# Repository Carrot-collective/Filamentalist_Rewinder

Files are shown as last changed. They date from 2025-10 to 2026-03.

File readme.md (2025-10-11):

## Carrot Collective Projects

[ERCF v3](https://github.com/Carrot-collective/ERCF_v3)

[ERCT / CottonTail](https://github.com/Carrot-collective/ERCT)

[Filametrix Toolhead Cutter Buffer](https://github.com/Carrot-collective/Filametrix)

[Blobifier Purge System](https://github.com/Carrot-collective/Blobifier)

[Filamentalist Rewinder Buffer](https://github.com/Carrot-collective/Filamentalist)

### Carrot Collective Affiliates

[Jabberwocky Toolhead](https://github.com/kinematicdigit/Jabberwocky)

[Happy Hare Wiki](https://github.com/moggieuk/Happy-Hare/wiki)

<br />

<p align="center">
<h1 align="center">The "Filamentalist" Passive Filament Driven Rewinder</h1>

[](https://github.com/Enraged-Rabbit-Community/ERCF_v2/tree/master/Recommended_Options/Filamentalist_Rewinder/Filamentalist_Classic_Rewinder)[](https://github.com/Enraged-Rabbit-Community/ERCF_v2/tree/master/Recommended_Options/Filamentalist_Rewinder/Filamentalist_FV3_Rewinder)[](https://github.com/Enraged-Rabbit-Community/ERCF_v2/tree/master/Recommended_Options/Filamentalist_Rewinder/Filamentalist_Enclosure)
</p>
   
## _____ [Filamentalist "Classic"](https://github.com/Enraged-Rabbit-Community/ERCF_v2/tree/master/Recommended_Options/Filamentalist_Rewinder/Filamentalist_Classic_Rewinder) _________ [Filamentalist FV3](https://github.com/Enraged-Rabbit-Community/ERCF_v2/tree/master/Recommended_Options/Filamentalist_Rewinder/Filamentalist_FV3_Rewinder) ___________[Filamentalist Enclosure](https://github.com/Enraged-Rabbit-Community/ERCF_v2/tree/master/Recommended_Options/Filamentalist_Rewinder/Filamentalist_Enclosure) ____
</p>

## Filamentalist Discord group [here:](https://discord.gg/zHGH9sXFVK) ##

##  Description & Theory of operation:

The Filamentalist is a passive (no motors or electronics required) integrated buffering and spool holding multi-material unit (MMU) solution.  It provides space savings and potential filament path reduction that comes with using paths from spool to buffer to MMU.

- The Filamentalist uses the axial force delivered by the MMU gear motor along the filament to load and unload to and from the filament spool.
- An adjustable spring clamp forces the filament against two o-rings that sit on the drive pulley to create a high traction interface for rotating the axle and filament spool.
- A one-way clutch style bearing locks against the drive shaft and rotates the filament spool to take up filament during an unload.
- For loading and print extruding, the clutch disengages allowing for effective free-spooling of the filament spool similar to a roller style spool holder.
- The difference in diameter of the filament driven clutched roller versus the larger rim roller that the filament spool sits on provides the needed gear ratio to produce enough rotations to take up, and unload a nearly empty or full filament roll.
- During unloading/buffering, to account for the varying diameter of a spool from full to empty, filament tension will cause the spring loaded arm to lift a small amount and release traction from the o-rings allowing slip to occur between the filament and the o-ring interface of the rewinder producing a dynamic, continuously modulating variable gear ratio (full spool = max slip, empty spool = no/minimal slip).

<p align="center">

</p>

<p align="center">


</p>

## Filamentalist Version Selection ##

One version is not necessarily better than the other.  The Filamentalist Classic has slightly better Tensioner system geometry making it a bit smoother in the filament grip/slip modulation.  The FV3 is "sexier" and accomodates wider spool widths in less horizontal space which can be useful for fitting in existing enclosures or across the top of a printer.  Below is a selection table to help with your decision.

<p align="center">

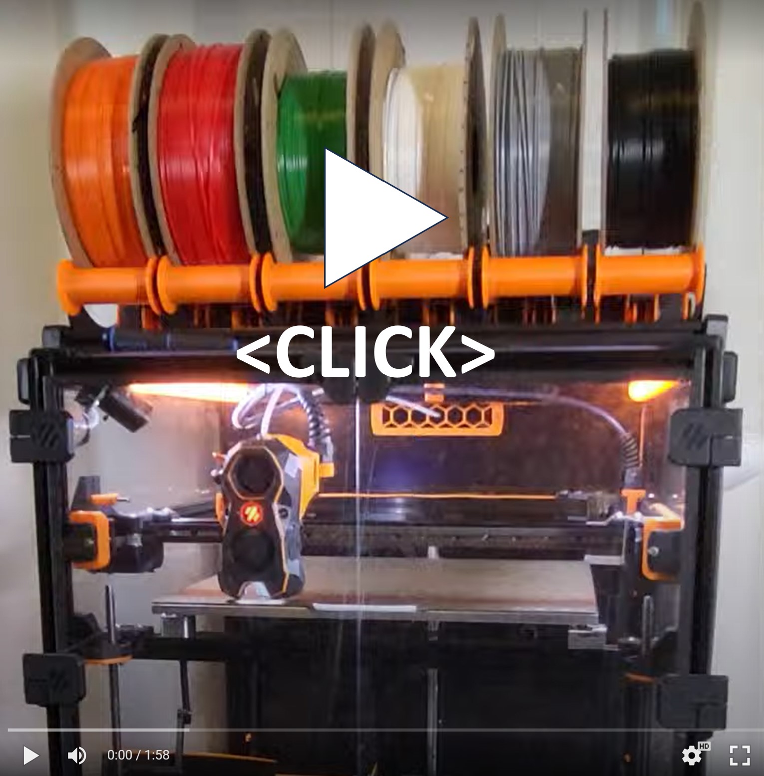
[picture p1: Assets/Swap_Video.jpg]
## Video of 6 rewinders swapping (plus SW Only Blobifier Purging):  [](https://photos.app.goo.gl/hKso7JYPZcdRLKrW8)

## [Video of loading a spool (pre-gate sensors auto-detect filament and pull into ERCF):](https://photos.app.goo.gl/yGS7Rr49dFMvjNLF9)  [](https://photos.app.goo.gl/yGS7Rr49dFMvjNLF9)

##  Credits:
Discord user Thisiscam first made me aware of [Muzi Xiaoyang's video](https://www.bilibili.com/video/BV1ZM41197fX/?spm_id_from=333.337.search-card.all.click) of a filament driven rewinder .  Through a long collaboration with Thisiscam, a great Beta dev/test team, and many design iterations/improvements on the Muzi Xiaoyang design, the Filamentalist was born. Key changes to the Muzi Xiaoyang design include incorporation of a one-way bearing, establishing the correct gear ratio for operation across the range of empty-to-full spools, and the long-life o-ring based filament clamping interface.

A special mention and thanks goes out to Cheesefrog and JCPhlux for their innovation and inputs for design refinement. 

##  **Additional Notes/Considerations** 

Things that you need to know include:
1. Due to continual evolution of the design based on user feedback, the pictures in the readme files and documentation may not always reflect the most current designs.  They will be similar and generally represent the latest parts and assemblies.
2. There are multiple options for the Filamentalist.  Determine which versions/options you want and select the stl's to print accordingly.  If you use Autodesk Fusion 360 there is parametric models available for both the Classic and FV3 rewinders that will allow customization for unique widths and axle lengths. Please see the Selection Aid table above to help choose.
3. If you're using, or upgrading from a ERCFv1 or v2 version you may want/need a higher torque gear motor.  Many in the Beta team ran NEMA 17's spec'd at 55 N-cm max torque and config'd them for 1-1.5A (probably overkill...).  If running the ERCF V1 or V2 with the 80 tooth gear Grafton's [40 Tooth NEMA 17 Mod](https://www.printables.com/model/692720-ercf-40-tooth-gear-modifiction) is a good modification for gaining more speed from a motor with 40N-cm torque or greater.  This may not be required so if you already have built your ERCF, try the Filamentalist with the motor/gearing you have and decide if you think you need more torque/speed.
4. Because the standard tuning of this design relies on some filament slip at the o-rings, the o-rings may ultimately wear-out.  Testing and extrapolation estimates that the wear-out point is  greater than 5K cycles. See the O-Ring Replacement section in the assembly manuals for o-ring swap/replacement instructions. 
5. Due to pressfits for the axle bearings and ECAS fitting, printer calibration is important.  Calibration "Test Block" stl's are included in the projects/CAD.  It is recommended you print the calibration tool first and test the press fits, M3 thread cutting, M3 slip fit, filament path holes to determine if you need to apply any scaling or changes to your extrusion factors in your slicer before printing.  Due to varying ECAS supplier tolerances and varying printer tolerances some experienced cracking at the ECAS hole when pressing in the ECAS.  If all other press fits work well on the calibration tool but you experience cracking at the ECAS hole when pressing in an ECAS fitting, you can use an Xacto knife to lightly remove some plastic from the ECAS hole.  If the ECAS is too loose you can use superglue to glue the ECAS into the Tensioner Mount (not the Test Block 😉 ).
6. Questions or input?
   - Refer to the [FAQ](https://github.com/Enraged-Rabbit-Community/ERCF_v2/blob/master/Recommended_Options/Filamentalist_Rewinder/Filamentalist_FAQ.md)
   - [Troubleshooting Guide](https://github.com/Enraged-Rabbit-Community/ERCF_v2/blob/master/Recommended_Options/Filamentalist_Rewinder/troubleshoot.md)
   - Filamentalist Discord group [here:](https://discord.gg/zHGH9sXFVK)

##  Tuning

Tune by setting the Tensioner Arm clamping force.  The arm does not need an extreme amount of tension.  To tune the spring force, lift the tensioner and insert a section of filament through the o-ring bearing interface and into the bowden tube.  Hold a Rim Roller to keep it from rotating and try to pull the filament out (in unload direction).  You want the slip force to be slightly more than what the overall system drag is, so you have to imagine the range of gear motor pull force vs rewinder drag and set a slip range in-between the two "imaginary" lines.  As a starting point adjust the spring tensioner screw accordingly and err on the light side.  Run the rewinder (see test code below). If loose filament is forming around the filament spool during unload, tighten the spring tensioning screw.  If no loose filament is forming around the filament roll, gradually reduce the spring tension until loose filament starts to accumulate and then increase tension in ~1/2 screw turn increments until you feel you have the lightest tension that results in a tightly packed unload. 

##  Testing

Below are macros you can cut and paste into the bottom of your mmu_software.cfg or printer.cfg to test and tune your rewinders.

Happy multi-material printing and rewindering!

```
[gcode_macro rewinder_test]
gcode:
    {% set tool = params.TOOL | default(0) | int %}   ; This target can be set with the drop-down in Mainsail
    {% set cycles = params.CYCLES | default(5) | int %}   ; This target can be set with the drop-down in Mainsail
    {% set speed = params.SPEED | default(300) | float %}   ; This target can be set with the drop-down in Mainsail
    {% set accel = params.ACCEL | default(300) | float %}   ; This target can be set with the drop-down in Mainsail
    {% set length = params.LENGTH | default(800) | float %}   ; This target can be set with the drop-down in Mainsail

    MMU_SELECT TOOL={tool}
    MMU_PRELOAD
    MMU_TEST_LOAD LENGTH=50
    {% for n in range(cycles) %}

        MMU_SERVO POS=DOWN
        MMU_TEST_MOVE SPEED={speed} ACCEL={accel} MOVE={length}
        MMU_SERVO POS=UP
# to stop a macro mid-cycle you must use the e-stop.  This dwell allows you to hit the e-stop while the servo is up so that you can pull the filament out of the ERCF while the printer/macro is stopped
        MMU_SERVO POS=DOWN
        MMU_TEST_MOVE SPEED={speed} ACCEL={accel} MOVE=-{length}
        MMU_SERVO POS=UP

    {% endfor %}

    MMU_UNLOAD

```

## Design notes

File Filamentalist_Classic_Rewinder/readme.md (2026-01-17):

<p align="center">
<h1 align="center">The Filamentalist "Classic" Passive Filament Driven Rewinder</h1>

<p align="center">]
</p>
   
## [Filamentalist Classic Assembly Guide Document](https://github.com/Enraged-Rabbit-Community/ERCF_v2/blob/a68bc6678bab41d7bded5e42a17276a9430a0f45/Recommended_Options/Filamentalist_Rewinder/Filamentalist_Classic/Do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)  [](https://github.com/Enraged-Rabbit-Community/ERCF_v2/blob/a68bc6678bab41d7bded5e42a17276a9430a0f45/Recommended_Options/Filamentalist_Rewinder/Filamentalist_Classic/Do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)

## [Filamentalist Classic Assembly Guide Video](https://youtu.be/-1cHOcnosxE?si=RZV318OI9f3f_CkE)  [](https://youtu.be/-1cHOcnosxE?si=RZV318OI9f3f_CkE)

##  **BOM:**

**ATTENTION!! PLEASE READ COMMENTS IN FAR RIGHT COLUMN** (you may need to scroll over in your view)

| Qty per Site | Part | Example Source Reference | Comments |
|---|---|---|---|
| 1 | 8mm dia. x 80mm Stainless Steel Dowell Pin | https://www.amazon.com/uxcell-Stainless-Chamfered-Support-Elements/dp/B0BC8VFSWD, Amazon Alternate https://www.amazon.com/Unifizz-Stainless-Steel-Round-Silver/dp/B09P9MC953?th=1 (sheared ends may need to be cleaned up), Aliexpress https://www.aliexpress.us/item/3256801518620991.html | Undersized shaft (7.93-7.97mm or 5/16" dia) works the best.  100mm length is more available and can extend out of rewinder, you can cut polished 8mm or 5/16" diameter stainless rod to length, or there are stls to make a wider rewinder based on a 100mm axle.  Custom rewinder widths are also possible using the Fusion 360 parametric model and you can cut shaft to whatever length is desired. 8mm (or 5/16") diameter straight stainless tube is also an excellent alternative to solid rods as the are much easier to cut to length. |
| 5 | MR608 bearings | Can be obtained anywhere (Home Depot, Amazon, Aliexpress, etc.)  | Inexpensive MR608-2RS rubber dust seal style is recommended as they are slightly higher resistance than the open, ZZ metal seal style, or plastic bearings. You actually want a little of resistance in the axle bearings to help the 1-way bearing unlock. |
| 1 | HF081412 One-Way Bearing | https://www.amazon.com/dp/B0C7TRFJBS, Aliexpress | 8mm Bore, 12mm length, 14.2mm Diameter. Get the "octogonal" style. |
| 1 | ECAS press-in pneumatic fittings for the bowden tubes (like used in ERCF)  |  | A locking clip is required and can be bought or printed (stl included).  The rubber seal is not needed and should not be installed upon assembly. |
| 2 | O-rings | Metric 3.5x20 (ID) or AS568 Standard size 211, Home Depot #110, Amazon example: https://www.amazon.com/211-Buna-N-Ring-Durometer-Black/dp/B000FN0W7I/, Aliexpress example: https://www.aliexpress.us/item/2255799953260685.html (select correct size) | In the range of 13/16" ID, 1-1/16" OD or ~20mm ID, ~27mm OD, ~3.5mm cross section/cs, Nitrile Butadiene Rubber (NBR or Buna-N)|
| 1 | Spring  | https://www.amazon.com/dp/B076LNJF5Q, Aliexpress | Like in extruders - 304 Stainless Steel,6mm OD,0.6mm Wire Size,7.5mm Compressed Length,15mm Free Length (the stiffer 1mm wire size extruder spring used on CW2 and G2E will also work if you have those on-hand) | |
| 1 | 3mm Heatset Insert | M3x4x5 like these:  https://www.amazon.com/gp/product/B09MCW7ZN5 | Voron standard size | set into the Tensioner Mnt |
| 1 | 3x35mm SHCS | SS Socket Head Cap Screw | Spring Tensioner Screw anything in the range of 35mm +/- 10mm should work.  If building the alernate reverse access version then a 30mm length is recommended. |
|  2-6  | M3x8 SHCS  |  Stainless Steel Socket Head Screw | for locking rim rollers to 8mm steel axle shaft.  1 to 3 screws per roller Depending on tightness/looseness of Rim Roller center bore |
| 6 | 3x12 FHCS  |  Stainless Steel Flat Head Screw | for Tensioner Mnt and Rear Axle installation 8/10/12mm lengths will work|
| 3 | 3x18 FHCS  |  Stainless Steel Flat Head Screw | for Tensioner Arm clamp bearings and Tensioner Mnt pivot installation 16mm length will work |
| 1 | M3 Washer  |  Stainless Steel | between Spring Tensioner screw head and spring |
| 4 | Rubber Band | See [FAQ](https://github.com/Enraged-Rabbit-Community/ERCF_v2/blob/master/Recommended_Options/Filamentalist_Rewinder/Filamentalist_FAQ.md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)) | bike tire inner tube or rubber bands |

**Optional Parts**
| Qty per Site | Part | Example Source Reference | Comments |
|---|---|---|---|
| 1 | D2F-L3 Microswitch  | Omron brand - Mouser, Digikey, etc., Aliexpress example: https://www.aliexpress.us/item/3256805036222979.html  | for pre-gate sensor option versions |
| 2 | M2x10 Self Tapping Screw | Philips or socket head.  Amazon example: https://www.amazon.com/DTGN-M2x10mm-Phillips-Self-tapping-Screw/dp/B0CSRTYBLR, Aliexpress example: https://www.aliexpress.us/item/3256802486141312.html (select size) | for pre-gate sensor option versions |
| 1 | JST-XH 2-pin Socket/Plug | Amazon example:  https://www.amazon.com/CQRobot-Connector-Terminals-Housing-Adapter/dp/B0B2R966ZY, Aliexpress Example: https://www.aliexpress.us/item/3256804799083128.html (need housing, plug, and terminal) | for pre-gate sensor option versions |
| var. | 24 awg wire  | | for pre-gate sensor option versions |
| var.  | 2.5mm ID PTFE tubing | Amazon, Aliexpress, 3D printing vendors | 2.5mm ID recommended but you can try whatever you have.  Length depends on the distance from your rewinder location to your ERCF inputs |

##  Printing Guidelines:

## **General:**
- Material: ABS or ASA (~170 gm per site)
- Print Time: ~8hr 17min (based on the Ellis PIF profile speeds, accelerations, and volumes)
- 0.2mm layer height
- 40% infill recommended.  Linear style infills are fastest (rectilinear, monotonic, grid, triangles, stars, etc.)
- Wall Count: 4
- Solid Top/Bottom Layers: 5

## **Part Specific:**
- Orientation suggestions are relative to the installed assembly orientation and are shown in the slicer images below.
- There are stls for both 80mm and 100mm wide version and a Fusion 360 parametric CAD model for additional custom widths.  See "Additional Notes/Considerations" point 3 above for more details.
- If rotating the Filamentalist is not feasible for your required filament loading direction or you need a bottom feed capability (for example enclosure limitations or feeding through the bottom of a shelf) there is an option for a rear loading version which only requires printing the Tensioner_Mount_Rear_Load_80mm/100mm_[option] in the place of Tensioner_Mount_80mm/100mm part.
  
  

- Stl's are provided for optional clip-in style supports where no Base_Plate is needed and the rewinders are easily clipped in and out of (2) 2020 extrusions mounted 170mm center-to-center apart.  This option is highly recommeded if your setup can accomodate this style type of mount.
  
  
- **!! IMPORTANT !!  This design relies on multiple press-fits for bearings and ECAS fittings.  As a result, printer calibration is important.  A Test_Block stl is included.  It is highly recommended that you print this block first, check fits, and make adjustments to extrusion multipliers and/or slicer scaling if needed before printing the Filamentalist parts.**
  
    

| **Qty per Site** | **Part**  | **Pic** |  **Orientation** | **Printed Supports Needed** | **Comments** |
|---|---|---|---|-----|---|
| 1 | Right_Support |  |  Horizontal | N | |
| 1 | Left_Support |  | Horizontal | N | |
| 1 | Option: Right_Support_[2020_Clip-In_option] |  |  Horizontal | N | |
| 1 | Option: Left_Support_[2020_Clip-In_option] |  | Horizontal | N | |
| 1 | Base_Plate_80mm/100mm_[option] |  | Horizontal | N | Optional part for a standalone unit not mounted to another surface  |
| 1 | Idler_Roller_Axle_80mm/100mm  |  | Horizontal | N | align flat of "D" to build plate |
| 2 | [a]_Rim_Roller_80mm/100mm |  | Horizontal | N | Dished side up. |
| 1 | [a]_Center_Drive_Roller  |  | Horizontal | N | Recommend scattered seams for press fit-bore concentricity |
| 2 | CDR_Spacer_80mm/100mm |   | Horizontal | N | |
| 1 | Tensioner_Arm_Left |   | Horizontal |  N |  |
| 1 | Tensioner_Arm_Right |   | Horizontal |  Built-in | Remove built-in support from the locking tab |
| 1 | [a]_Tensioner_Mount_80mm/100mm |  | Vertical (as installed) | N  | There is a pre-gate sensor option version available as well (split to parts in slicer for print-in-place breakaway connector retaining key).  |
| 1 | [a]_Tensioner_Mount_Rear_Load_80mm/100mm _[option] |  | Vertical (as installed).  Optional for rear loading if needed. | N  | There is a pre-gate sensor option version available as well.  |
| 1 | [a]_Idler_Roller _(male) _80mm/100mm |   | Vertical  | N  |  Scattered seams |
| 1 | [a]_Idler_Roller _(female)_80mm/100mm |   | Vertical  | N  |  Scattered seams |
| 1 | Axle_Depth_Tool_80mm/100mm |  | Vertical | N | Pocket opening up.  Print with 100% infill for reuse strength and durability when building multiple rewinders. |
| 2 | [a]_ECAS_Clip |  |  Horizontal | N | Tab up |
| 1 | Test_Block |  |  608 Pocket facing up | N | printer calibration tool |

##  Tuning

Tune by setting the Tensioner Arm clamping force.  The arm does not need an extreme amount of tension.  To tune the spring force, lift the tensioner and insert a section of filament through the o-ring bearing interface and into the bowden tube.  Hold the center roller by placing your thumb against the o-rings and try to pull the filament out.  You want the slip force to be slightly more than what the overall system drag is, so you have to imagine the range of gear motor pull force vs rewinder drag and set a slip range in-between the two "imaginary" lines.  Adjust the spring tensioner screw accordingly and err on the light side.  Run the rewinder (see test code below). If loose filament is forming around the filament spool during unload, tighten the spring tensioning screw.  If no loose filament is forming around the filament roll, gradually reduce the spring tension until loose filament starts to accumulate and then increase tension in ~1/2 screw turn increments until you feel you have the lightest tension that results in a tightly packed unload. 

##  O-Ring Replacement

You may never need to replace o-rings.  Testing and extrapolation estimates that the wear-out point is ~5K cycles.  The impact of o-ring wear-out can be reduced by periodically swapping highly used rewinders with low use rewinders in your line-up.  Also, o-rings with grooves worn in them can be swapped with their opposing partners to present the unworn side/face to the filament to extend the life of a set.  For o-ring replacement, remove the Drive Roller Assembly from the rewinder (unscrew the (6) screws of the Right and Left Supports).  Then unscrew the set screw on one Rim Roller.  You can now slide the CDR Spacer and Center Drive Roller from the axle, remove the old o-rings (a dental pic works great), and install a pair of new ones.  Reinstall the Center Drive Roller and CDR Spacer back on the axle and install the Rim Roller back onto the axle per 3.3 above, and re-install the supports.  

##  Troubleshooting

Please see [troubleshooting guide](troubleshoot.md), reference the [FAQ](Filamentalist_FAQ.md), or join our discord server (https://discord.gg/uDcGxukRKd) for more help.

#  Version History

Versioning convention.  V"X"."Y"."Z"
- "X" represents a major change in form, fit, or function.  An increment in "X" may not require that existing built units undergo rework but the new parts will generally not be compatible with past version rewinders.
- "Y" represents a "step rev" or minor revision.  These are generally small "tweaks" for improved functionality, useability, and/or assembly and typically would not require reprint/rework for existing rewinders.  
- "Z" represents a backwards compatible "bug fix".  This will generally be addressing nuisance CAD or printability issues.

V1 - 5/17/24 - Public release into ERCF V2 RC2 repository

V1.1 - 5/19/24 - Update to CAD and stls for Tensioner Arms to remove potential filament catching point during endless spool ejection

V1.2 - 5/20/24 - Reverted Center_Drive_Roller to cylindrical press fit hole (vs hex of V1 and V1.1).  Revised 608 press fit pockets of Idler_Roller_(male&female) parts for both 80mm and 100mm width versions for improved press fit.

V1.3 - 5/20/24 - Added bevel to internal step on  Idler_Roller_(male) part for 80mm and 100mm versions to improve printability.  Updated the .f3dparametric file, step files, and stls for 80mm and 100mm versions.

V1.4 - 5/21/24 - Shortened threads on Idler_Roller_male parts by 1.5mm to remove slight interference.  Updated CAD, 80mm, and 100mm stls.

V1.5 - 6/4/24 - Slightly deepened 608 bearing pockets in Idler Roller parts to prevent potential side loading binding due to print/assembly tolerances.  Reprint not required for existing functioning units.

V1.6 - 6/12/24 - No mandatory reprints/rebuilds required:  Updated CAD parametric model and 80/100mm step files because two  Tensioner Mount-to-Support holes were getting "buried" in the 100mm version.  Updated the Tensioner_Mount_100mm stl file as well.

V1.7 - 6/13/24 - Opened up c-sunk hole on Tensioner_Arm_Left part pivot screw hole to allow for full seating of a FHCS head and use of a 16mm long screw.  A new stl for Tensioner_Arm_Left ans new f3d and step files are included.

V1.8 - 7/2/24 - Removed notch/gap in axle pressing tool that shouldn't have been there.  80/100mm stl's updated as well as f3d and stp CAD files.

V2 - 7/22/24
  1. Added Rear Load option Tensioner_Mount (works as bottom load too)
  2. Removed threaded Rim Roller option and converted Rim Rollers from press-fit to set screw style.
  3. Add 608 bearing inner race clearance back into Supports.
  4. Added ~2mm of additional bowden capture in Tensioner_Mounts

V3 - 8/5/24
  1.  Add options for Tensioner Mounts with pre-Gate sensors
  2.  Included option for the Filamentalist Enclosure style Base Supports
  3.  Updated all supports to include a spool guide rail to help keep spools from wandering off of the rollers.

V3.0.1 - 8/8/24 - No reprint/rebuild required:
1. Improved clearances for indexing tab feature in Tensioner Arm parts
2. Improved breakaway feature for small print-in support in Tensioner_Arm_Right part 
3. Provided additional edge chamfering to Idler Roller Axles
4. Reinstated design history in Filamentalist_(parametric)_V3.f3d CAD model so that the parametric functionality would work correctly.
5. Added accent color to file naming convention in stl file names.
6. Updated pdf manual to reflect/describe accent color for file naming convention in stl file names.

V3.0.2 - 8/15/24 - No reprint/rebuild required:
1. Added more reference dimensions to the User Parameters section for the Filamentalist_(parametric).f3d parametric CAD model.

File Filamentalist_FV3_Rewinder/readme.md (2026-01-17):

<p align="center">
<h1 align="center">The Filamentalist V3 ("FV3") Passive Filament Driven Rewinder</h1>
<p align="center">

</p>

## [FV3 Assembly Guide Document](https://github.com/Enraged-Rabbit-Community/ERCF_v2/blob/master/Recommended_Options/Filamentalist_Rewinder/Filamentalist_FV3_Rewinder/Documentation/Filamentalist_V3_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)  [](https://github.com/Enraged-Rabbit-Community/ERCF_v2/blob/master/Recommended_Options/Filamentalist_Rewinder/Filamentalist_FV3_Rewinder/Documentation/Filamentalist_V3_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)
##  **BOM:**

**ATTENTION!! PLEASE READ COMMENTS IN FAR RIGHT COLUMN** (you may need to scroll over in your view)

| Qty per Site | Part | Example Source Reference | Comments |
|---|---|---|---|
| 1 | 8mm dia. x ##mm Stainless Steel Rod, Tube, or Dowell Pin | https://www.amazon.com/uxcell-Stainless-Chamfered-Support-Elements/dp/B0BC8T7ZQB?th=1, Aliexpress https://www.aliexpress.us/item/2255800287548941.html (select M8x70mm) | Undersized shaft (7.93-7.97mm or 5/16" dia) works the best.  50mm axles will work in the standard width design but longer axles cut to length (up to ~75mm) will provide greater stability for the Rim Rollers.  The Classic Filamentalist 80mm axles will work but hang over ~1mm per side.  Custom rewinder widths are possible using the Fusion 360 parametric model and you can cut shaft to whatever length is desired.  8mm (or 5/16") diameter straight stainless tube is also an excellent alternative to solid rods as they are much easier to cut to length like https://www.amazon.com/uxcell-Stainless-Thickness-Seamless-Straight/dp/B081GBTQGC or https://www.aliexpress.us/item/3256805495613016.html. |
| 1 | 688 bearing | For Tensioner Arm|
| 4 | 608 bearings | For Drive and Idler axles.  Can be obtained anywhere (Home Depot, Amazon, Aliexpress, etc.)  | Inexpensive MR608-2RS rubber dust seal style is recommended as they are slightly higher resistance than the open, ZZ metal seal style, or plastic bearings. You actually want a little of resistance in the axle bearings to help the 1-way bearing unlock. |
   OR:
|   4   | 688 bearings | As an alternative to the 608 bearings for Drive and Idler axles, so would be a total of 5 688 bearings including the Tensioner Arm bearing.  This allows for only needing to buy one bearing size but the 688's might be a tighter fit on the axle shafts.  Inexpensive MR688-2RS rubber dust seal style is recommended as they are slightly higher resistance than the open, ZZ metal seal style, or plastic bearings. You actually want a little of resistance in the axle bearings to help the 1-way bearing unlock. |
|   1   | HF081412 One-Way Bearing | https://www.amazon.com/dp/B0C7TRFJBS, Aliexpress | 8mm Bore, 12mm length, 14.2mm Diameter. Get the "octogonal" style. |
|   1   | ECAS04   |  | Press-in pneumatic fitting for the bowden tubes (like used in ERCF).  A locking clip is required and can be bought or printed (stl included).  The rubber seal is not needed and should not be installed upon assembly. |
|   2   | O-ring | Metric 3.5x20 (ID) or AS568 Standard size 211, Home Depot #110, Amazon example: https://www.amazon.com/211-Buna-N-Ring-Durometer-Black/dp/B000FN0W7I/, Aliexpress example: https://www.aliexpress.us/item/2255799953260685.html (select correct size) | In the range of 13/16" ID, 1-1/16" OD or ~20mm ID, ~27mm OD, ~3.5mm cross section/cs, Nitrile Butadiene Rubber (NBR or Buna-N)|
|   1   | Spring  |  https:https://www.amazon.com/dp/B076LNJF5Q, Aliexpress https://www.aliexpress.us/item/3256805126192641.html (select size per comments) | 304 Stainless Steel,6mm OD,0.6mm Wire Size,7.5mm Compressed Length,15mm Free Length |                                 |
|   1 | 3mm Heatset Insert | M3x4x5 like these:  https://www.amazon.com/gp/product/B09MCW7ZN5 | Voron standard size | set into the Tensioner Mnt |
|   1   | M3x30mm SHCS | SS Socket Head Cap Screw | Spring Tensioner Screw |
|  6-10  | M3x12-16mm SHCS  |  12-16mm length will work | for locking rim rollers to 8mm steel axle shaft.  1 to 3 screws per roller Depending on tightness/looseness of Rim Roller center bore.  4 additional screws if using the Filamentalist Enclosure Mounts |
|  4  | M3x12 FHCS  |  Flat Head Cap Screw | for Idler Roller wheels, Tensioner Bearing axle, and Tensioner Pivot |
|   12-14   | M3x8mm FHCS  |  Stainless Steel Flat Head Cap Screw | Qty 12 for 2020 center mount, 14 for Enclosure mount |
|   1   | M3 Washer  |  Stainless Steel | for Spring Tensioner screw |
|   4   | #84 Rubber Band | See [FAQ](https://github.com/Enraged-Rabbit-Community/ERCF_v2/blob/master/Recommended_Options/Filamentalist_Rewinder/Filamentalist_FAQ.md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) | 2" bike tire inner tube cut to width or rubber bands |

**Parts for Microswitch Option**
| Qty per Site | Part | Example Source Reference | Comments |
|---|---|---|---|
| 1 | Omron D2F-01FL-D3 Lever Microswitch | https://www.mouser.com/ProductDetail/Omron-Electronics/D2F-01FL-D3?qs=i1w9Bv2NFd2YXdp4zNwbgA%3D%3D  | For pre-gate sensor levered switch option. |
   OR:
|   1   | Omron D2F-01F-D3 Button Microswitch | https://www.mouser.com/ProductDetail/Omron-Electronics/D2F-01F-D3?qs=i1w9Bv2NFd2sPdBLm34BPQ%3D%3D  | For pre-gate sensor printed lever switch option. |
|   1   | MR85 Bearing | Amazon: https://www.amazon.com/dp/B07CKL54RS, Aliexpress: https://www.aliexpress.us/item/3256807026256776.html   | ZZ, RS, or open style will work.  For pre-gate sensor switch option. |
   OR:
|   1   | 8x3 Disc Magnet | Amazon: https://www.amazon.com/FINDMAG-Magnetic-Whiteboard-Refrigerator-Magnets-8x3mm/dp/B0863BGG6H, Aliexpress: https://www.aliexpress.us/item/3256806495856656.html   | For pre-gate sensor switch option. |
   OR:
|   1   | 6x3 Disc Magnet | Amazon: https://www.amazon.com/TRYMAG-Magnets-Refrigerator-Whiteboard-Neodymium/dp/B09QHSB2XM, Aliexpress: https://www.aliexpress.us/item/3256807048616464.html   | For pre-gate sensor switch option. |  
|   var.   | 24 awg wire  |   | for pre-gate sensor option versions |
|   2   | M2x8mm SHCS |  Amazon:  https://www.amazon.com/Alloy-Steel-Socket-Screws-Black/dp/B015A37DVU, Aliexpress:  https://www.aliexpress.us/item/3256806889548681.html | Self tapping screws can be used as an alternative |
| 2  | Male/Female connectors |  | Connectors of your choice, JST-XH 2-pin works well |

##  Printing Guidelines:

## **General:**
- Material: ABS or ASA (2020 Center Mount version: ~154gm per unit, Filamentalist Enclsoure Mount Version: ~175gm per unit)
- Print Time: 2020 Center Mount version: ~7hr 34min, Filamentalist Enclsoure Mount Version: ~9hr 10min (based on the Ellis PIF profile speeds, accelerations, and volumes)
- 0.2mm layer height
- 40% infill recommended.  Linear style infills are fastest (rectilinear, monotonic, grid, triangles, stars, etc.)
- Wall Count: 4
- Solid Top/Bottom Layers: 5

- Recommended orientation is set in the stl files and should load correctly into slicer programs.  Print orientation is shown below in the slicer plate pictures for base and accent color parts.
- Where applicable, stl's are provided for two different axle bearing types, 688 (16mm OD) and 608 (22mm OD) bearings.  Bearing size is denoted in the file naming.
- **!! IMPORTANT !!  This design relies on multiple press-fits for bearings and ECAS fittings.  As a result, printer calibration is important.  The Print_Calibration_Tool_###_Bearing.stl file is included.  It is highly recommended that you print this part first, check fits, and make adjustments to extrusion multipliers and/or slicer scaling if needed before printing the Filamentalist parts.**
   - Other materials such as PETG or PLA may work fine but parts were not designed or validated for these materials.  If you want to use a different material start with the Print Calibration Tool and adjust extrusion rates and slicer scaling to achieve the correct dimensions for the press fit parts.



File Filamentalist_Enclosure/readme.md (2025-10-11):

# The "Filamentalist" Enclosure # 

The Filamentalist Enclosure is a passive dry box designed to house the Filamentalist passive rewinder.  It  consists of (4) printed endcaps, (6) pieces of 2020 extrusion cut/ordered to the desired length, and 0.060" (1/16') polycarbonate sheet(s) cut to size. Enclosure specific Filamentalist supports are required (these are included in the Filamentalist optional stl's as well as under the Enclosure stl directory).


</p>


</p>


</p>


</p>


</p>


</p>

BOM:

- 2020 Extrusion - Qty 6 - Select/cut length to be greater than or equal to [Rewinder Qty] X [Rewinder Width] + 10mm
    - for example: 6 X 81.5 (std. Filamentalist Width) + 10 = 499mm.  Round up to a standard 500mm long 2020 extrusion
    - get extrusions with holes that can be tapped to a 5mm thread (like the Misumi with a 4.2mm D hole)
    - examples: https://www.amazon.com/dp/B09DYMCBYF, https://www.aliexpress.us/item/3256801651139612.html

- Polycarbonate Sheet (Lexan) - 1/16" (also 0.060" or 1.5mm) thick.  Width of pieces = Extrusion Length -2mm (i.e. cut sheet to 498mm wide if using 500mm extrusions)
    - Lid Length = 451.5mm
    - Base Rear Panel Height = 120mm
    - Base Front Panel Height = 45mm
    - Bottom Panel Length (if used) = 230mm
    - For enclosures up to 607.6mm wide a single 24" x 36" sheet is enough material.
      - (2) 24" x 24" or (1) 24" x 24" + (2) 12" x 24" sheets will work as well if it is easier for you to source smaller sheets.
    - Sourcing Alternatives:
      - If there are difficulties sourcing the recommended Polycarbonate (Lexan) sheet material, PET and PET-G sheet has been used successfully although it wil be less scratch resistant
      - 2mm sheet can also be substituted but it will be more difficult when bending the lid panel into the lid frame and end caps

- Seal Material - ~10m or 32ft of 3/8" wide x 1/4" high (9mm x 6mm) self-adhesive weather seal.  Something like this:  https://www.homedepot.com/p/M-D-Building-Products-17-ft-Black-Small-Rubber-Auto-Marine-Weatherseal-for-All-Climates-01025/202066509, or https://www.amazon.com/Insulation-Weatherproof-Soundproofing-Self-Adhesive-Weatherstrip/dp/B082HDZ1P1?th=1, or https://www.aliexpress.us/item/3256806396445681.html.  Most of the glue needs to be peeled off so you want the style that has the "strings" embedded in the glue to aid in removal.

- M5x10/12mm length BHCS or SHCS - Qty 6 - For securing end caps to extrusions.  BHCS (Button Head) looks the best.

- M5 10mm length BHCS - Qty 4 - for mounting hinges to base and lid frames

- M5 x 16/18/20mm length BHCS - Qty 2 - Hinge Pin Screws.

- M3 x 4/5mm length BHCS or SHCS - Qty 2 - for tying lid panel to lid endcaps.

- 5mm Heatset Insert - Qty 2 - Optional, for setting how far the lid hinges back.

- M5 x 8/10mm length SHCS - Qty 2 - Optional, for setting how far the lid hinges back.
  
- 6mm OD/4mm ID grommets for sealing  bowden tubes. Drill 6.5mm holes.  Example:  https://a.co/d/bBc6JAL

(6) standard width (81.5mm) Filamentalist will fit in the 500mm length extrusion version of the enclosure.  There is room, and some special "far left" and "far right" extended supports that allow you to build one ~94mm wide Filamentalist unit using the parametric model to support a wider spool like KVP or NinjaFlex.

**Assembly Tips:**

**Lid Panel Installation:** The 0.060" Lexan bends easily but it is not easy to bend it and get it captured in the lid endcaps and extrusions.  Its a two person job. If doing it alone use 2 or 3 loops of string, or even better adjustable straps, set at a length to hold the correct bend and spacing at the edges of the Lexan.  Secure the non-captured end of the extrusions with a loop or strip of tape so that you don't spread/overflex the extrusions and potentially crack the endcap while installing the curved Lexan.

**Seal Installation:**


</p>

</p>

</p>

</p>

</p>

**Securing/Sealing on Printer:**

For a Voron enclosure you can "straddle" the top panel like the pic below.  Drill 2 countersunk holes in the top panel and screw them into t-nuts in the bottom enclosure extrusion.  The screw heads sit just below the panel surface so that the bowden tube doesnt catch on them while the print head is zooming around.   Run seal material in the rear bottom extrusion channel of the enclosure. Cut out sections of the weather stripping base to make space for the t-nuts to sit under but leave a continuous piece of weatherstripping seal running over the top of the t-nuts.  You can stick toothpicks into the t-nut holes (or 3mm screws with the heads cut off) to serve as locating pegs when you drop the enclosure onto the printer to make sure the top panel holes align with the t-nut locations.  This will pull  the top panel against the seal and is enough to secure the enclosure in place on the printer.



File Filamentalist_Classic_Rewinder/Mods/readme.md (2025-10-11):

# Mods

User mods for the Filamentalist Passive Rewinder

## Table structure

---

| Creator | Mod title | Description |
| --- | --- | --- |
|v6cl|[Filamentalist_F1](https://github.com/Enraged-Rabbit-Community/ERCF_v2/tree/master/Recommended_Options/Filamentalist_Rewinder/User_Mods/Filamentalist_F1mod) | Cool F1 race car vibe that mounts on a single 2020 extrusion rail.  Version 0.2 uses magnets instead of a spring for the Tensioner.
|SkiBikeMake|[Filamentalist_Enclosure](https://github.com/Enraged-Rabbit-Community/ERCF_v2/tree/master/Recommended_Options/Filamentalist_Rewinder/User_Mods/Filamentalist_Enclosure) | A simple, yet elegant passive dry enclosure for Filamentalist Rewinders.
|SkiBikeMake|[Fully_Printed_Filamentalist](https://github.com/Enraged-Rabbit-Community/ERCF_v2/tree/master/Recommended_Options/Filamentalist_Rewinder/User_Mods/Fully_Printed_Filamentalist) | A fully functional Filamentalist Rewinder that incorporates a printed 1-way clutch and Drive Roller Axle.
---

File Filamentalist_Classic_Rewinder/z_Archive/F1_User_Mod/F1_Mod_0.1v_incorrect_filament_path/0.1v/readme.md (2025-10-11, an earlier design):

forked from (https://github.com/SkiBikePrint/ERCF_Mods/tree/main/Filamentalist)

# BOM

- 608 Bearing x 5
- HF081412 One-Way Bearing
- Rubber O - ring ID ~20mm , OD ~27mm AN-211
- 623 Bearing x 2 (Optional)
- ECAS04
- Ball pen Spring 20mm (https://ko.aliexpress.com/w/wholesale-ball-pen-spring.html?spm=a2g0o.detail.search.0)
- 55mm ~ 60mm Length , 8mm Diameter shaft or dowell pin
- 3mm insert nut
- M3 Socket head bolts
- M3 Flat head bolts
- silicone bracelet or rubber band of appropriate width and size.(Optional) (https://www.amazon.com/dp/B0CPJPN41V?th=1)
- PTFE Tube OD 4mm, ID 2.5mm or 3mm

# Filamentalist F1

## Changes and Improvements

- Use M3 insert nut and add 623 bearing(2ea)

- The fixing method of the front wheel has been changed from press fit to bolt method for disassembly/assembly.
Improved convenience

- Easy to attach and detach from one 2020 profile (Small parts that can be placed on a flat surface will be added later)
  
- Designed part size so that it can be printed on a 180x180 size bed.

- Hole on the front to check the condition of the O-ring

- Can be replaced with wider wheels to accommodate wider spools (Wheels of various widths, fixed and released with 2 bolts)

- It uses the spring used in a typical ballpoint pen.









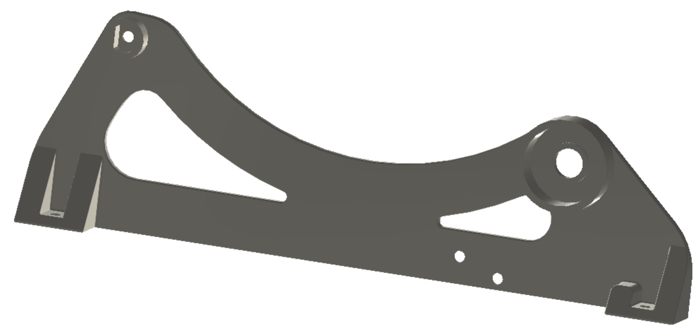
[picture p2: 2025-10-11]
Assets/Right_Support.jpg

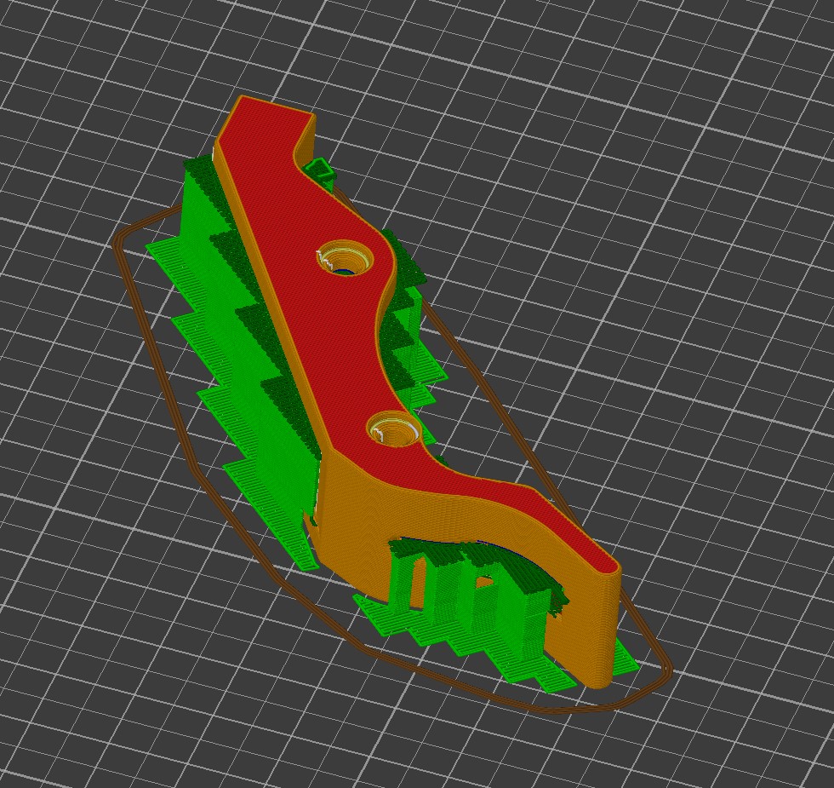
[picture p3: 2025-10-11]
Assets/Tensioner_Arm Supports.jpg

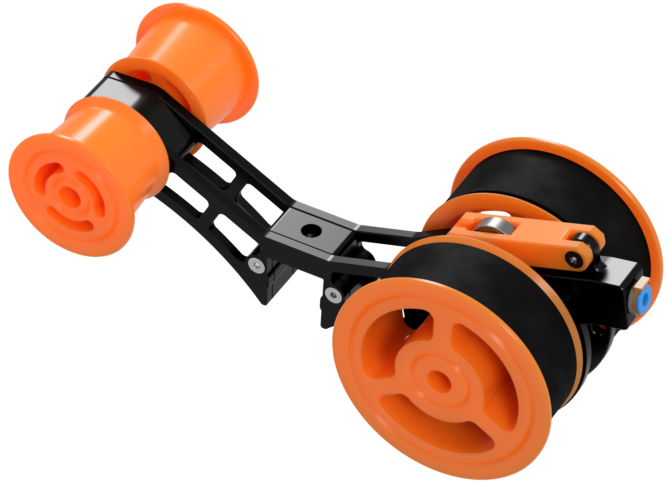
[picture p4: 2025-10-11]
Assets/FV3/Filamentalist_V3_Render_Large.png

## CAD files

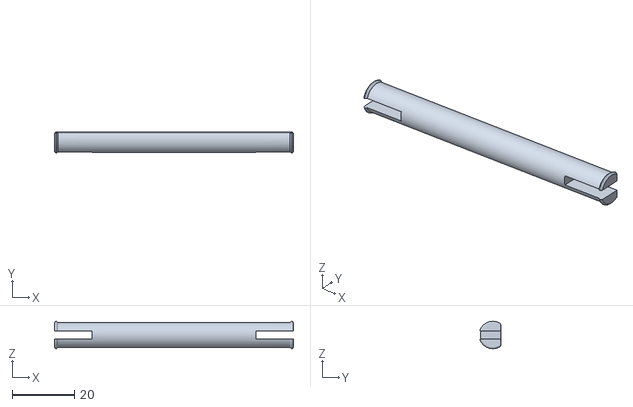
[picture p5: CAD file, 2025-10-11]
Filamentalist_Classic_Rewinder/Mods/Fully_Printed_Filamentalist/stls/80mm_Axle/Roller_Axle_X2_80mm_V1.stl
76.5 x 6.84 x 8.81

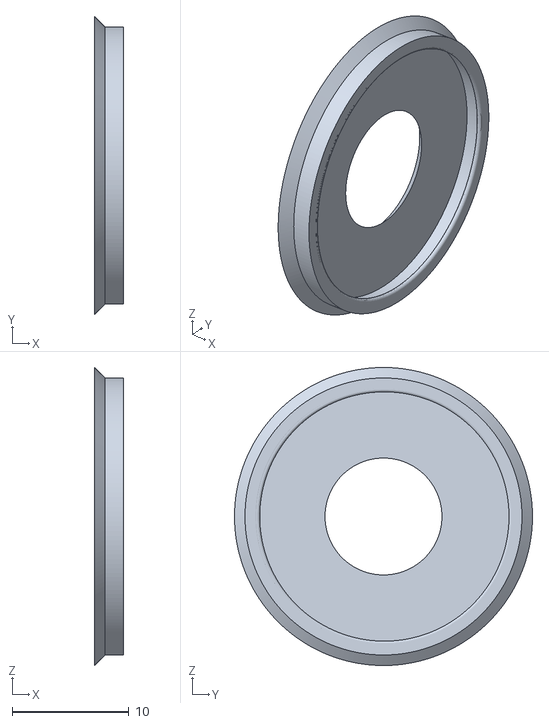
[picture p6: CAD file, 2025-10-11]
Filamentalist_Classic_Rewinder/Mods/Fully_Printed_Filamentalist/stls/Clutch_Cover_V1.stl
2.47 x 25.5 x 25.5

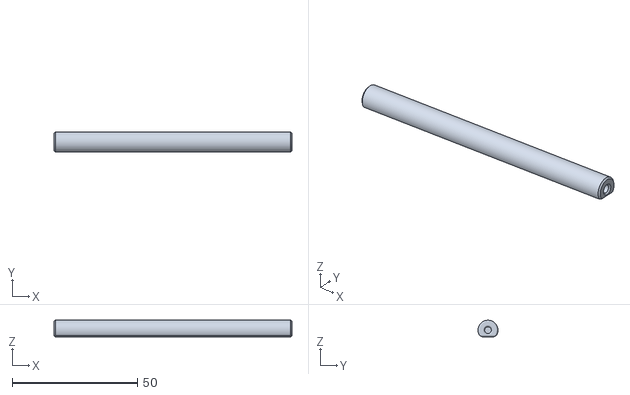
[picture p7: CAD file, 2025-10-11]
Filamentalist_Classic_Rewinder/Stls/100mm_Axle/Idler_Roller_Axle_100mm.stl
95.0 x 8.00 x 6.65

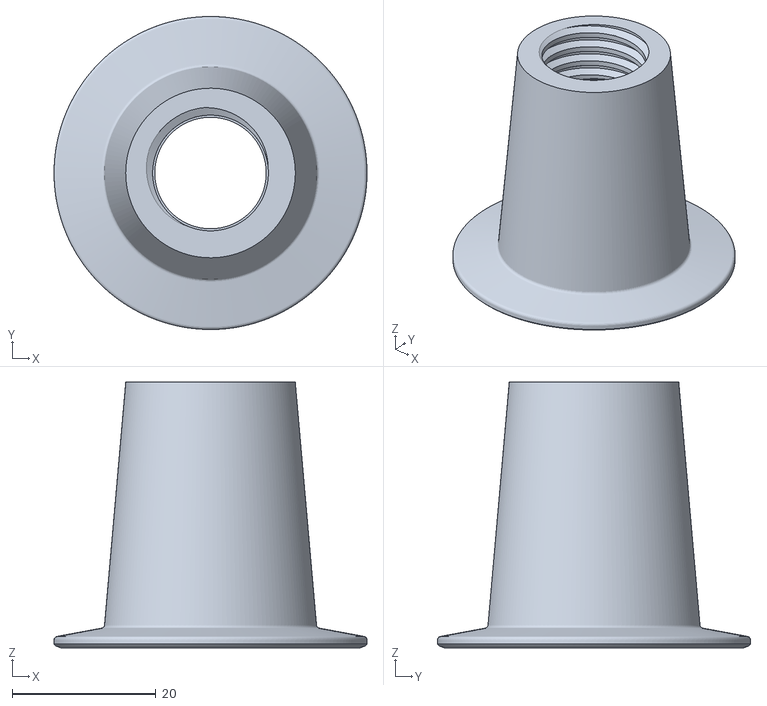
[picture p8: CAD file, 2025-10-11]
Filamentalist_Classic_Rewinder/Stls/80mm_Axle/[a]_Idler_Roller_(female)_80mm.stl
43.6 x 43.6 x 37.0

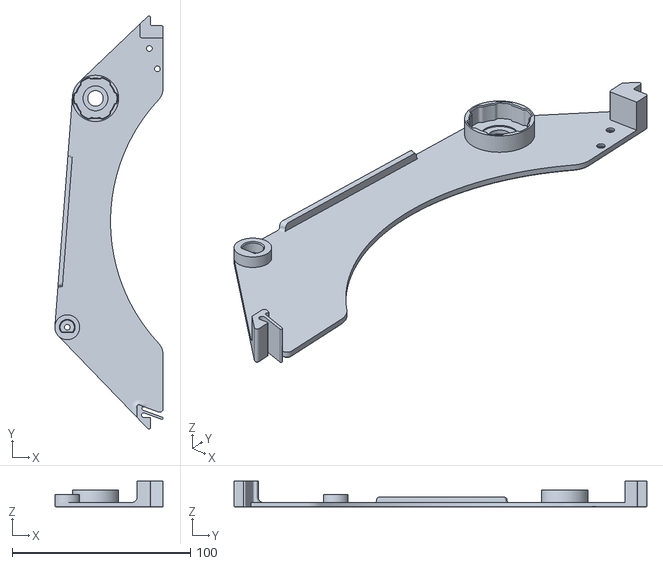
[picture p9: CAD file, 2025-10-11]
Filamentalist_Classic_Rewinder/Stls/Support_Filamentalist_Enclosure_Left_[option].stl
60.8 x 231.9 x 14.5

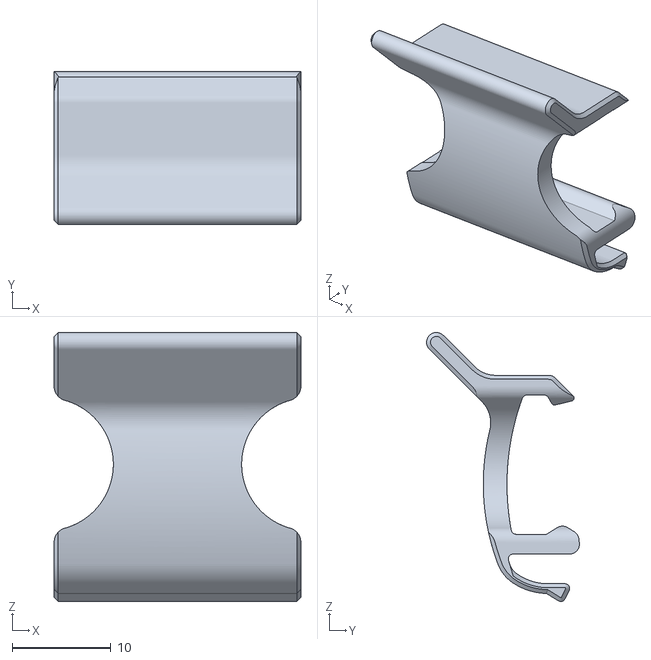
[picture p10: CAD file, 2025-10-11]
Filamentalist_Enclosure/Stls/Latch_Lid.stl
25.0 x 15.5 x 27.2

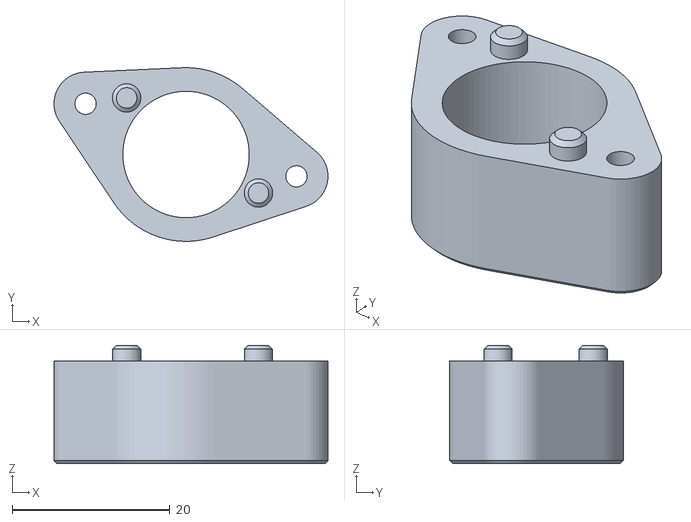
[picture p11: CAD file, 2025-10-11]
Filamentalist_FV3_Rewinder/Stls/Chassis/2020_Center_Rail_Mount_[option]/2020_Mnt_Rear_Spacer_688_Bearing_[option].stl
34.7 x 22.0 x 15.0

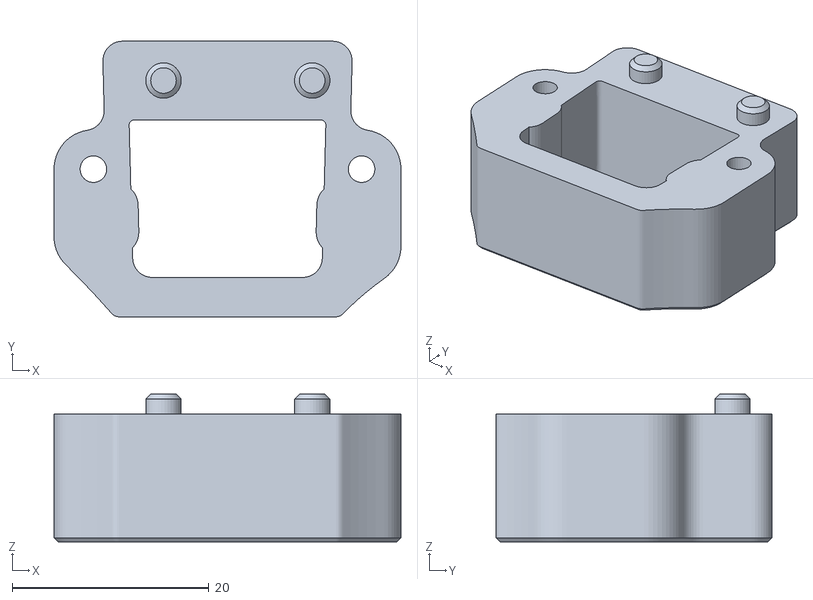
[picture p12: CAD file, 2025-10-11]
Filamentalist_FV3_Rewinder/Stls/Chassis/Chassis_Cntr_Spacer.stl
35.2 x 28.0 x 15.0

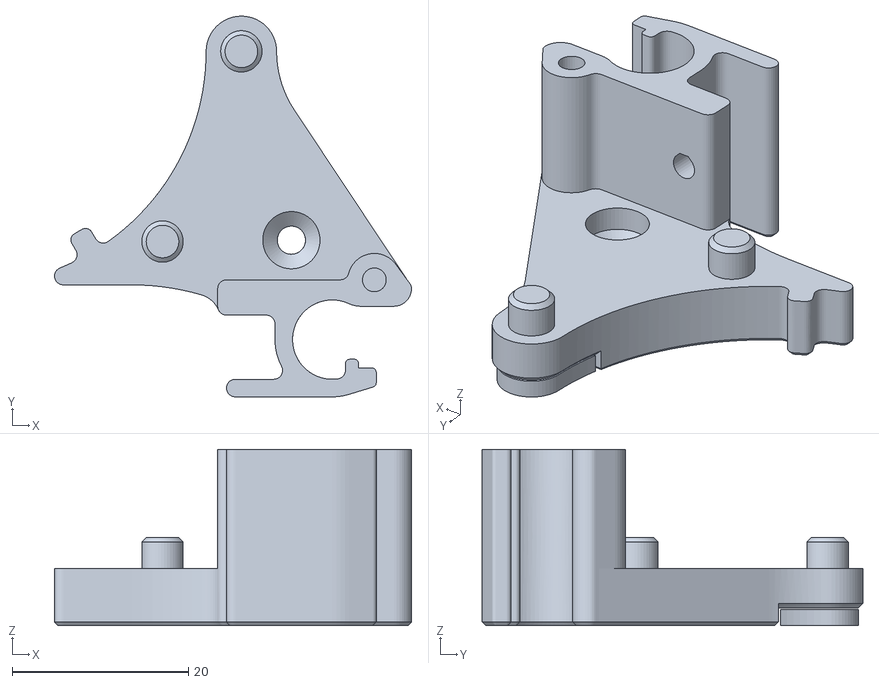
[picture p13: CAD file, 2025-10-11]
Filamentalist_FV3_Rewinder/Stls/Chassis/Filamentalist_Enclosure_Mnt_[option]/Fil_Encl_Frnt_R_[option].stl
40.5 x 43.2 x 20.0

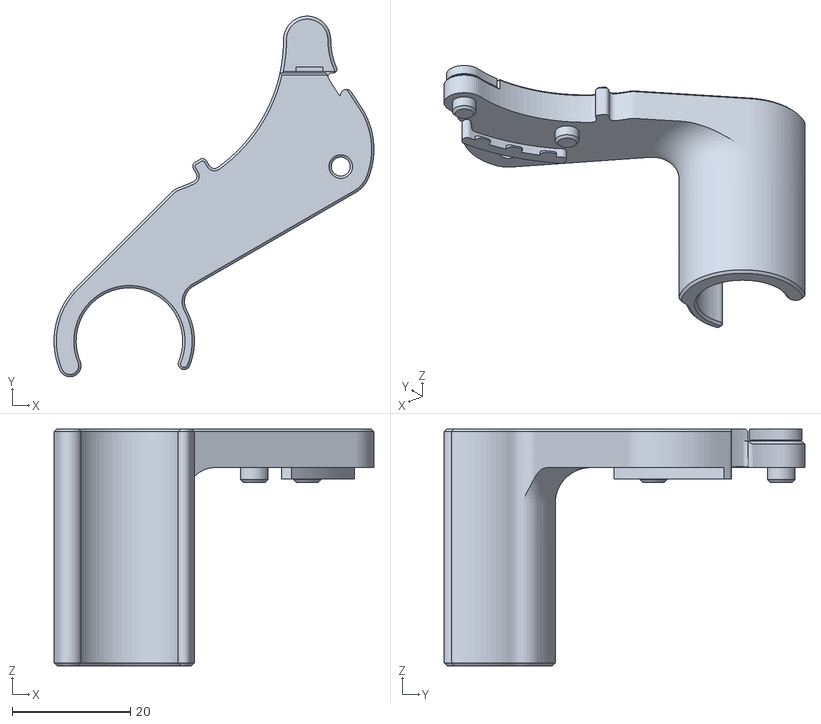
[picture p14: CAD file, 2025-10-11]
Filamentalist_FV3_Rewinder/Stls/Chassis/RepRak_Mount_Assy/RepRak_Mnt_Front_L_[option].stl
54.1 x 61.0 x 40.0

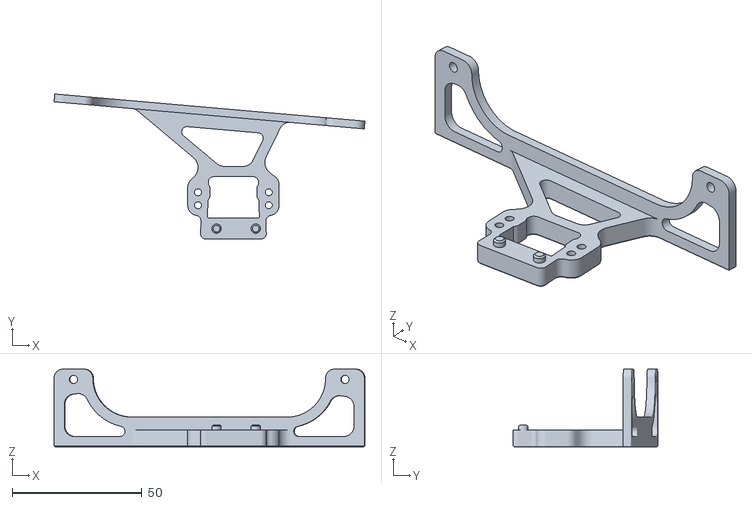
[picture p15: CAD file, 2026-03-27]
Filamentalist_FV3_Rewinder/Stls/Chassis/Rubbermaind_21cup_Dry_Box/Rubbermaid_21cup_Dry_Box_Mount_L_[option].stl
119.8 x 55.9 x 30.0

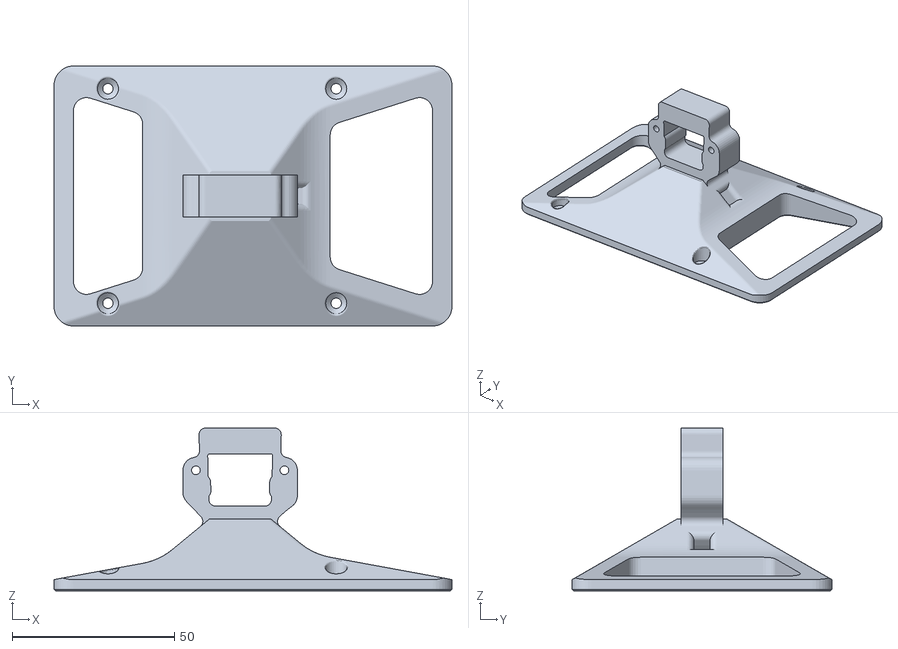
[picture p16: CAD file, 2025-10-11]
Filamentalist_FV3_Rewinder/Stls/Chassis/Standalone_Mount_Assy/Center_Mount_Version/Standalone_Cntr_Mnt_[option].stl
122.5 x 80.0 x 50.1

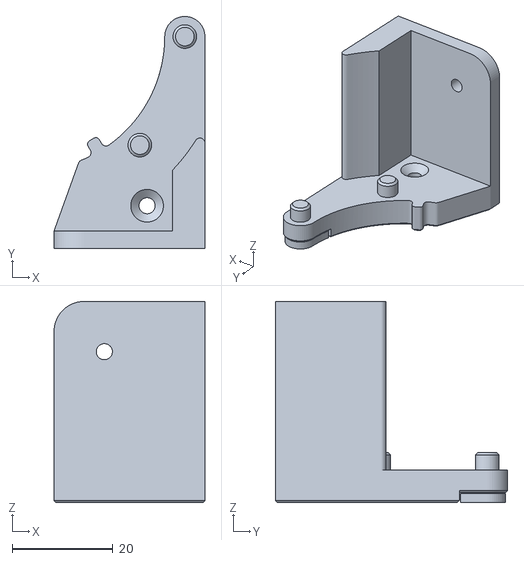
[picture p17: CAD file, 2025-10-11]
Filamentalist_FV3_Rewinder/Stls/Chassis/Standalone_Mount_Assy/Front_Rear_Mount_Version/Standalone_Mnt_Front_R_[option].stl
30.0 x 46.1 x 40.0

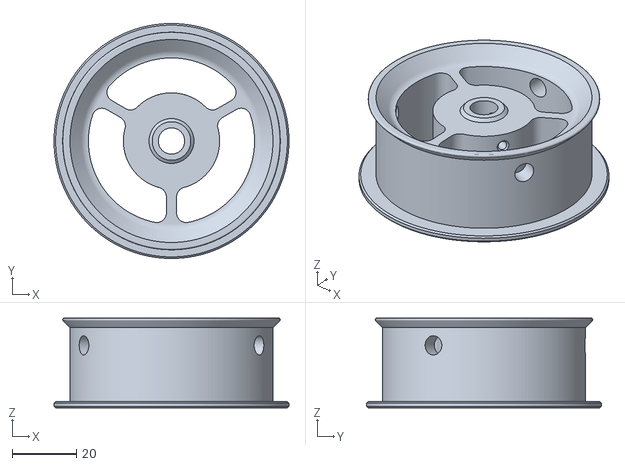
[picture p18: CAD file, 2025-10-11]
Filamentalist_FV3_Rewinder/Stls/Drive_Roller_Assy/[a]_Rim_Roller_608_Bearing_x2.stl
73.2 x 73.2 x 28.0

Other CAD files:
Filamentalist_FV3_Rewinder/Stls/Drive_Roller_Assy/CDR_Printed_Clutch_Assy_[option]/Axle_Bearing_Printed_688_Bearing_x2_[option].stl
Filamentalist_FV3_Rewinder/Stls/Idler_Roller_Assy/Idler_Roller_Axle.stl
Filamentalist_FV3_Rewinder/Stls/Tensioner_Mount_Assy/ECAS_Clip_[optional_print].stl
Filamentalist_FV3_Rewinder/Stls/Tensioner_Mount_Assy/Tensioner_Mount_Microswitch_[option]/Printed_Switch_Lever.stl
Filamentalist_Classic_Rewinder/Mods/Fully_Printed_Filamentalist/stls/80mm_Axle/CDR_Spacer_80mm_x2_V1.stl
Filamentalist_Classic_Rewinder/Mods/Fully_Printed_Filamentalist/stls/80mm_Axle/Idler_Roller_(female)_80mm_V1.stl
Filamentalist_Classic_Rewinder/Mods/Fully_Printed_Filamentalist/stls/80mm_Axle/Idler_Roller_(male)_80mm_V1.stl
Filamentalist_Classic_Rewinder/Mods/Fully_Printed_Filamentalist/stls/80mm_Axle/Rim_Roller_x2_80mm_V1.stl
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

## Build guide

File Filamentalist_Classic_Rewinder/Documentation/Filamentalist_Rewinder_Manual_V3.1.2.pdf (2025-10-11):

# ERCF

### Video Assembly Guide Here! (https://youtu.be/5Qk3N2sKz40)

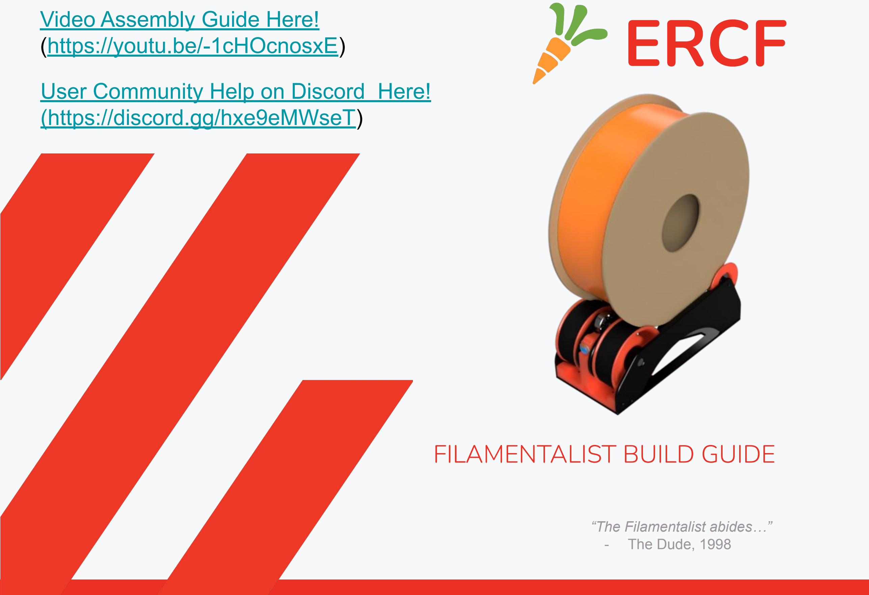
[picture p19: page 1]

# FILAMENTALIST BUILD GUIDE

“The Filamentalist abides…”
- The Dude, 1998

### (https://youtu.be/-1cHOcnosxE)

### User Community Help on Discord Here! (https://youtu.be/5Qk3N2sKz40) (https://discord.gg/hxe9eMWseT)

ENRAGED RABBIT CARROT FEEDER (ERCF)

Enraged Rabbit Filamentalist Rewinder CAD version: V3

2 | 2

FILAMENTALIST

Introduction
Theory of Operation | 3
Acknowledgements | 4
Configuration/Options | 5
Part Printing Guidelines | 7
STL File Naming Key | 9
Hardware Reference | 10
Required Tools | 11
CAD Files and Parametric Model | 14

## TABLE OF CONTENTS

Assembly | 18
Drive Roller | 19
Idler Roller | 22
Tensioner Mount | 24
Base | 29
Tuning | 35
O-Ring Replacement | 36
Questions, Troubleshooting, and Help | 37

Be Kind Rewind
–2008 starring Jack Black and Mos Def

ENRAGED RABBIT CARROT FEEDER (ERCF)

### INTRODUCTION

The Filamentalist is an integrated solution for buffering and spool holding, providing space savings as well as the potential for filament path reduction, and the associated drag/resistance that comes with long runs from spool to buffer to MMU.
- The Filamentalist uses the axial force delivered by the MMU gear motor along the filament to load and unload to and from the filament spool.
- An adjustable spring clamp forces the filament against two o-rings that sit on the drive pulley to create a high traction interface, for rotating the axle and filament spool.
- A one-way clutch style bearing locks against the drive shaft and rotates the filament spool, to take up filament during an unload.
- For loading and print extruding, the clutch disengages allowing for effective free-spooling of the filament spool similar to a roller style spool holder.
- The difference in diameter of the filament driven clutched roller versus the larger roller that the filament spool sits on provides the needed gear ratio to produce enough rotations to take up, and unload a nearly empty or full filament roll.
- During unloading/buffering, to account for the varying diameter of a spool from full to empty filament tension will cause the spring loaded arm to lift a small amount and release traction from the o-rings allowing slip to occur between the filament and the o-ring interface of the rewinder (full spool = max slip, empty spool = no/minimal slip).

THEORY OF OPERATION

ONE-WAY BEARING

O-RING/FILAMENT
INTERFACE

GEAR RATIO FOR
EMPTY-TO-FULL
SPOOL RANGE

ENRAGED RABBIT CARROT FEEDER (ERCF)

### INTRODUCTION

I would like to acknowledgement and thank:
Thisiscam who shared Muzi Xiaoyang's video of a filament driven rewinder and then continued to partner and share his brilliance in the evolution and optimization of the final product.

The Beta Test Team who provided design validation and innumerous inputs for design improvements, printability, and simplification of assembly.
Cheesefrog
Grafton
Biokeks
Meltiseugen
and many more…

All the Early Adopters who allowed a fleet of hundreds of rewinders to help further refine the Filamentalist, the documentation, and volume unit validation. You know who you are!
The ERCF Team for building, supporting, and allowing me to be part of this amazing ecosystem of multi-material printing solutions! Your creativity, commitment, professionalism, collaboration, generosity, and sense of community is an inspiration!

ACKNOWLEDGEMENTS

ENRAGED RABBIT CARROT FEEDER (ERCF)

Things that you need to know include:

There are multiple options for the Filamentalist. Determine which versions/options you want and select the stl's to print accordingly.

- Unit Width: 80mm, 100mm, and custom width via Fusion 360 parametric model
- Mounting Style: Standard (shelf) mount, 2020 rail clip-in mount, 2020 clip-in mount for Filamentalist Enclosure

Based on your mounting needs, you may or may not need to print and install the Base Plate part. It is really only needed if you don't plan to attach the rewinder to a surface.

Feed Direction: The orientation of your MMU with respect to your filament spools location may require a front, rear, or bottom loading capability from the rewinder. Tensioner Mount options are provided to support this.

Pre-gate Sensors: If your MMU does not have pre-gate sensors, and the software you use supports them (like Happy Hare), there are CottonTail pre-gate sensors and Filamentalist Tensioner Mount options that support this.

If you are using, or upgrading from an ERCFv1 or v2 RC1A version you may want/need a higher torque gear motor. Many in the Beta team ran NEMA 17's spec'd at 55 N-cm max torque and config'd them for 1-1.5A (probably overkill...). Grafton's 40 Tooth NEMA 17 Mod (https://www.printables.com/model/692720-ercf-40-tooth-gear-modifiction) is a good addition for gaining more speed from a high torque motor. This may not be required, so if you already have built your ERCF, try the Filamentalist with the motor/gearing you have and decide if you need more torque/speed.

INTRODUCTION

CONFIGURATION/OPTIONS CONSIDERATIONS

ENRAGED RABBIT CARROT FEEDER (ERCF)

The “standard” Filamentalist has an 80mm axle and supports a maximum spool width of 68mm and supports most standard 1, 0.5, and 0.25KG spool sizes and still be able to fit 6 rewinders across the top of a 350 size Voron printer. Some spools such as NinjaFlex and KVP's are too wide to fit the 80mm design. If you use spools wider than 68mm there is also step and stl files posted for a 100mm axle length version. If you are using Autodesk Fusion 360, the provided .f3d file in the CAD directory is a parametric based model allowing you to customize the width of your rewinder to suit your max/min spool widths and/or to design around a standard available steel axle length (see Parametric CAD Model section in this document).

Because the standard tuning of this design relies on some filament slip at the o-rings, the o-rings may ultimately wear-out. Testing and extrapolation estimates that the wear-out point is ~5K cycles. See the O-Ring Replacement section at the end of this document for o-ring swap/replacement instructions.

Questions or input?

Refer to the:

Filamentalist FAQ (https://github.com/Enraged-Rabbit-Community/ERCF_v2/blob/master/Recommended_Options/Filamentalist_Rewinder/Filamentalist_FAQ.md)

Troubleshooting Guide (https://github.com/Enraged-Rabbit-Community/ERCF_v2/blob/master/Recommended_Options/Filamentalist_Rewinder/troubleshoot.md)

Filamentalist Discord Channel (https://discord.gg/uDcGxukRKd)

Enjoy the process of building as much as utilizing your Enraged Rabbit Carrot Feeder (ERCF) and Filamentalist Rewinder!

INTRODUCTION

CONFIGURATION/OPTIONS CONSIDERATIONS (continued)

ENRAGED RABBIT CARROT FEEDER (ERCF)

The ERCF team has provided the following print guidelines. We recommend you to follow them in order to have the best chance at success with your parts. There are often questions about substituting materials or changing printing standards, but we recommend you follow these.

The majority of mechanical issues users experience with the ERCF and its supporting components can be traced back to print quality and and accuracy. Please take the time to print the calibration tools and dial in your printer before moving forward.

INTRODUCTION

FDM MATERIAL
The Filamentalist was designed for, and
tested with ABS and ASA. Based on the tolerance requirements of the design we recommend to only use ABS OR ASA.

INFILL TYPE
Grid, Gyroid, Honeycomb, Triangle or Cubic.

LAYER HEIGHT
Recommended : 0.2mm
First Layer: 0.25mm

INFILL PERCENTAGE
Recommended: 40%

EXTRUSION WIDTH
Recommended : Forced 0.4mm

WALL COUNT
Recommended : 4

SOLID TOP/BOTTOM LAYERS
Recommended : 5

### PART PRINTING GUIDELINES

ENRAGED RABBIT CARROT FEEDER (ERCF)

IMPORTANT !! The Filamentalist design relies on multiple press-fits for bearings and ECAS fittings. As a result, printer calibration is important. A Test_Block stl is included. It is highly recommended that you print this block first, check fits, and make adjustments to extrusion multipliers and/or slicer scaling if needed before printing the Filamentalist parts.

INTRODUCTION

### THE TEST BLOCK CALIBRATION TOOL

Test_Block.stl

M3 Thread Cutting Hole

ECAS Hole

608 Bearing Hole

TESTS
Insert the different pieces of hardware in their dedicated positions: ECAS fitting, M3 screw thread in, and 608 bearing.

The ECAS fitting should be a tight, snap-in fit. If the plastic cracks after ECAS insertion due to too tight a fit or the ECAS is a loose fit then extrusion rates and/or interior hole settings need to be adjusted in your slicer. You may need to cut the print with clippers to remove the ECAS.

You should be able to hand press in a 608 bearing into the pocket. It is acceptable if additional force, like light hammer taps is required to fully seat the bearing. The bearing can be removed by inserting an 8mm axle/rod through the bearing and rocking the rod back and forth while gently pulling on the rod, “walking” the bearing out of the pocket.

Screw an M3 screw into the back side (opposite ECAS hole). The screw should tightly screw in and cut threads into the plastic. If the ECAS and 608 bearing press in nicely but this hole is tight, no print adjustments need to be made but M3 screw holes may need to be opened up hand turning a 2.5mm drill bit.

ECAS

608 Bearing

ENRAGED RABBIT CARROT FEEDER (ERCF)

FILE NAMING
By this time you should have already downloaded our STL files from the ERCF GitHub. This is how to use the naming conventions.

Part_Name]_[Width_Version]_[Quantity_Required]_[option].stl

Example [a]_Rim_Roller_80mm_x2.stl

INTRODUCTION

PRIMARY COLOR
Example Left_Support.stl
These files will have nothing at the start of the filename.

ACCENT COLOR
Example
[a]_Center_Drive_Roller.stl These files have an ‘’[a]_’’ prefix to denote that they should be printed with an
accent color.

WIDTH VERSION
Filenames with an ‘’80mm’’ or “100mm” after the file
name are specific to the
width option you choose to build.

QUANTITY REQUIRED
Filenames ending with ‘’_x#’’ are telling you the quantity of that part required to build a single rewinder

STL FILE NAMING KEY

[option]
Filenames with an ‘“[option]”after the filename or width are build options/alternatives such as:
- Clip-In style mount
- Supports for the Filamentalist Enclosure
- Pre-gate sensors included in Tensioner Mounts

ENRAGED RABBIT CARROT FEEDER (ERCF)

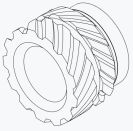
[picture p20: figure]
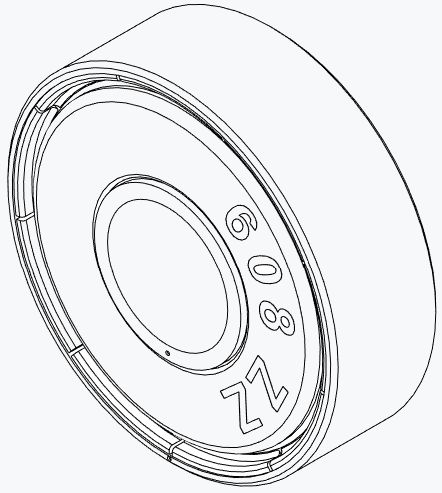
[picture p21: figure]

10 | 10

INTRODUCTION

FLAT HEAD COUNTERSUNK SCREW (FHCS)
Metric fastener with a cone shaped head and a flat top.

ISO 10642

SOCKET HEAD CAP SCREW (SHCS) Metric fastener with a cylindrical head and hex drive. The most common fastener used on the ERCF.

ISO 4762

WASHER
Plain metal stamped washer.

DIN 125

SELF TAPPING SCREW
Fastener with a pronounced thread profile that is screwed directly into plastic. Used with optional pre-gate sensor Filamentalist version.

HEAT SET INSERT
Brass, threaded, with ridges on the outside. Heat to approx 250C with soldering iron and push into a hole in the plastic. Plastic cools and solidifies around the knurls/ridges for excellent resistance to torque and pull-out.

608 BEARING
For the Filamentalist, the 2RS (sealed) style is preferred but can be used with the open or ZZ (shielded) style.

ECAS FITTING
4mm Push -Fit PTFE tubing fitting.

SPRING
For the Filamentalist, 304 Stainless Steel,6mm OD, 0.6-1mm Wire Size, 15mm Free Length spring used in Tensioner Assembly.

HARDWARE REFERENCE

ENRAGED RABBIT CARROT FEEDER (ERCF)

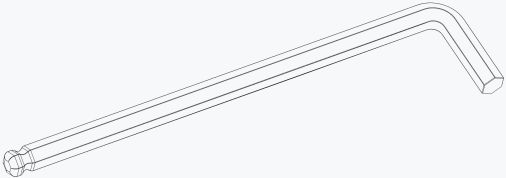
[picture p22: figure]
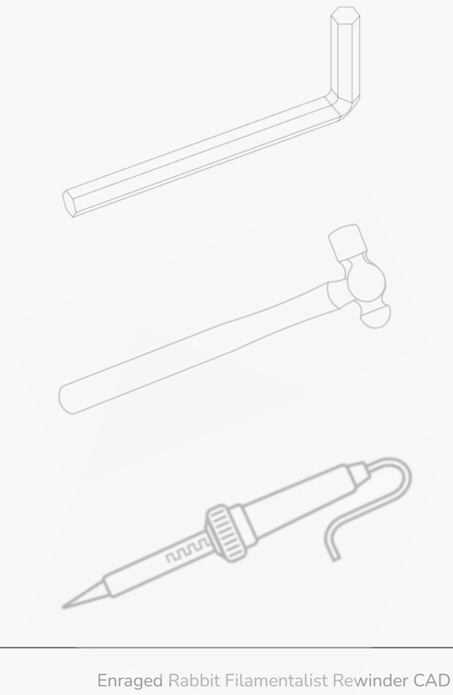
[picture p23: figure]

11 | 11

INTRODUCTION

BALL-END HEX DRIVER
Adjustment of the Tensioner screw in this design benefits from the use of a 2.5mm ball-end hex driver.

2MM HEX DRIVER
The 2mm hex driver will see a lot of use in this build. A quality driver is strongly recommended. Refer to the sourcing guide for suggestions.

SOLDERING IRON
For the insertion of the single heat set insert in the Tensioner Mount part of the Filamentalist rewinder

SMALL HAMMER
A small hammer my be useful/required to tap in press-fit bearings.

TOOLS

ENRAGED RABBIT CARROT FEEDER (ERCF)

12 | 12
INTRODUCTION | TOOLS

ANGLE GRINDER/DREMEL
For cutting 8mm axle rods/tubes to length if
required.
VISE
A vise is handy cutting 8mm axles.
CAD SOFTWARE
Filamentalist_80mm/100mm.step or Filamentalist_(parametric).f3d
Software is a tool too! The CAD file for the Filamentalist was designed to be used along with this manual as a supplement or reference, even if you aren’t a CAD Pro. You can use the free edition of Fusion360, or your choice of CAD program such as TinkerCAD, onshape, or FreeCAD.
SUPERGLUE
Yes, we consider this a tool. Superglue may be useful if your print tolerances result in slip-fits for the bearings and ECAS. Cheap, single-use gel tubes are fine.

TEST BLOCK TOOL
ERCFv2/Recommended_Options/Filamentalist_Re winder/Stls/Test_Block.stl
It is highly recommended that you print this Test_Block.stl part first, check fits of M3 screws, 608 bearings, and the ECAS fitting, and make adjustments to extrusion multipliers and/or slicer scaling if needed before printing the Filamentalist parts.
AXLE DEPTH TOOL
ERCFv2/Recommended_Options/Filamentalist_Re winder/Stls/##mm_Axle/Axle_Depth_Tool.stl Helps you set the depth that the Rim Roller parts are attached on the axle to ensure free floating CDR Spacer parts and the correct overall width of the rewinder.

ENRAGED RABBIT CARROT FEEDER (ERCF)

If you need assistance with your build you can head over the Filamentalist Discord group and post your questions in the ercf_questions channel. It is the primary medium to help people with their ERCF build and tuning! You can also check the Github page for the latest releases.

INTRODUCTION

### Discord Link (https://discord.gg/uDcGxukRKd)

GitHub Link (https://github.com/Enraged-Rabbit-Community/ERCF_v2/tree/master/Recommended_Options/Filamentalist_Rewinder)

HOW TO GET HELP

ENRAGED RABBIT CARROT FEEDER (ERCF)

We have provided the Filamentalist CAD files (ERCFv2/Recommended_Options/Filamentalist_Rewinder/CAD/Filamentalist_##mm.step and Filamentalist_(parametric).f3d), so that you can follow along with the instructions in a 3D view, if you like.

The CAD file is organized into folders based on the instructions in this manual. First hide all the parts, and then reveal the parts up to the step you are on in this manual, and the CAD should match what you are building.

All of the non-printed parts are in each section’s Hardware folder.

INTRODUCTION

USING THE CAD FILES

ENRAGED RABBIT CARROT FEEDER (ERCF)

If you are using Autodesk Fusion 360 the “Filamentalist_(parametric).f3d file provided in the CAD folder is a parametric based model allowing you to customize the width of your rewinder to suit your max/min spool widths and/or to design around a standard available steel axle length. The model will update and accurately show the results of these parameters to help you visualize the acceptability of the result as well as provide reference dimensions to aid in part sourcing.
To customize your Filamentalist width and axle sizing, load the model, make sure you are in the "Solid" menu, and then select "Modify" and "Change Parameters"

INTRODUCTION

THE PARAMETRIC CAD MODEL

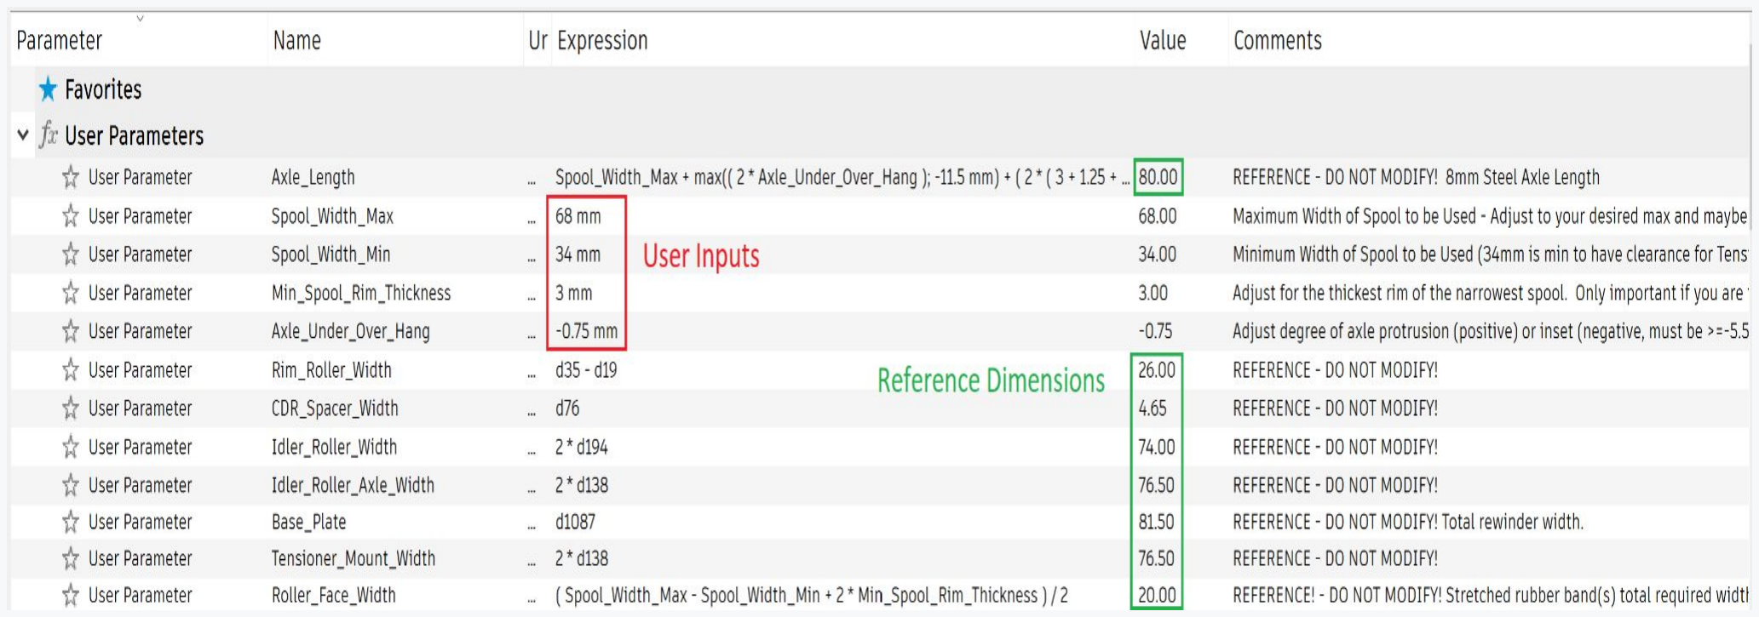
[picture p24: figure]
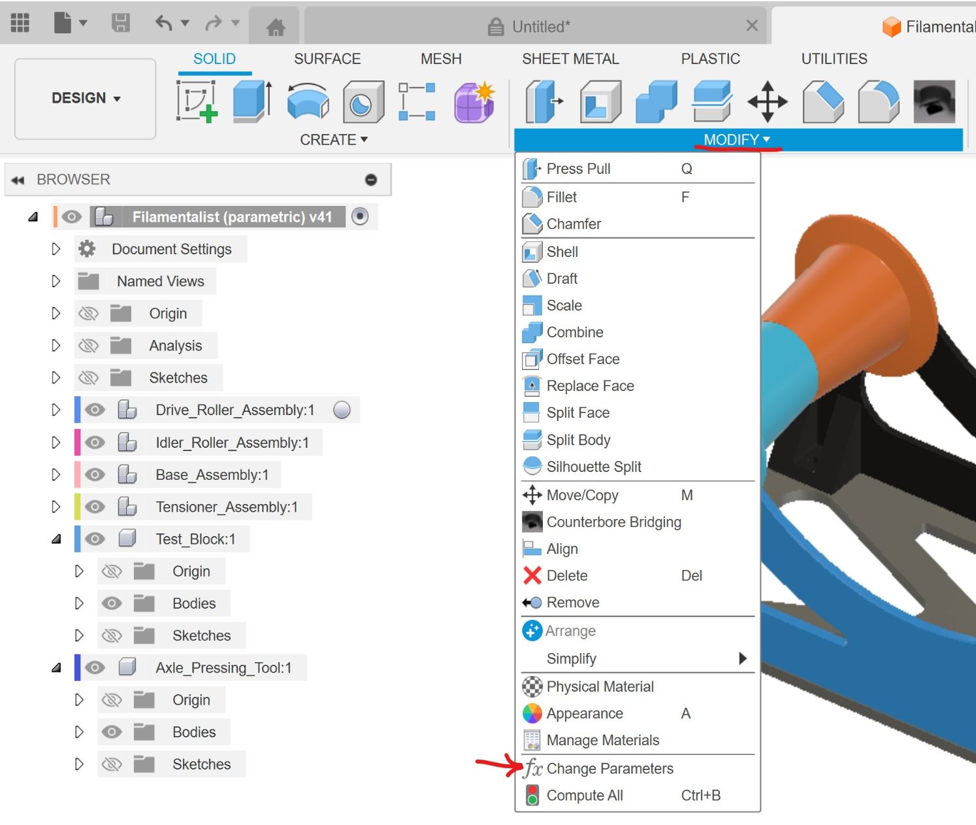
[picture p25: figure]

Adjust the following parameters to meet your needs:
Spool_Width_Max - Set this to accommodate the widest filament spool you expect to use. It is recommended to add ~2mm to this number to allow for spool width and rim straightness/variation.

(parameter descriptions continued on next page)

ENRAGED RABBIT CARROT FEEDER (ERCF)

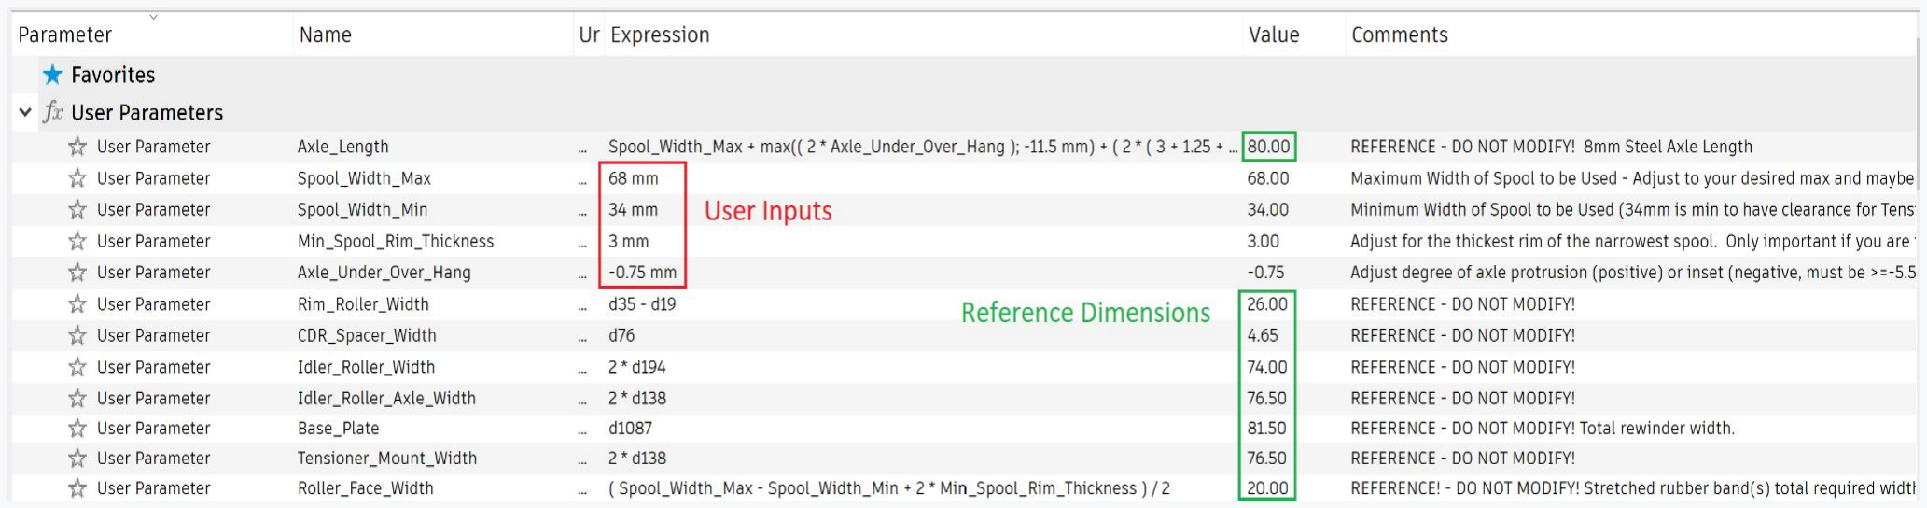
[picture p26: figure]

16 | 16

INTRODUCTION

THE PARAMETRIC CAD MODEL (continued)

Adjust the following parameters to meet your needs (continued from previous page):
Spool_Width_Min - Set this to accommodate the narrowest filament spool you expect to use. Due to the width of the Tensioner Assembly the minimum spool width is constrained at 34mm and will default to this number if you enter something less than 34mm. If you don't expect to use narrow spools (like 250kg or 500kg spools) you can set this to a larger number to produce narrower Rim Rollers. Narrower Rim Rollers will reduce print time and filament consumed and may allow for usage of more standard, less expensive, and/or fewer rubber bands but will limit overall future flexibility of your rewinder.

Min_Spool_Rim_Thickness - Normally this can be left at the default of 3mm but if you are trying to squeeze narrow spools onto the rewinder, you are close to that 34mm minimum width, and your narrow spool rims are less than 3mm thick, you can adjust for your thickest rim of your narrowest spool to make it fit the rewinder.

ENRAGED RABBIT CARROT FEEDER (ERCF)

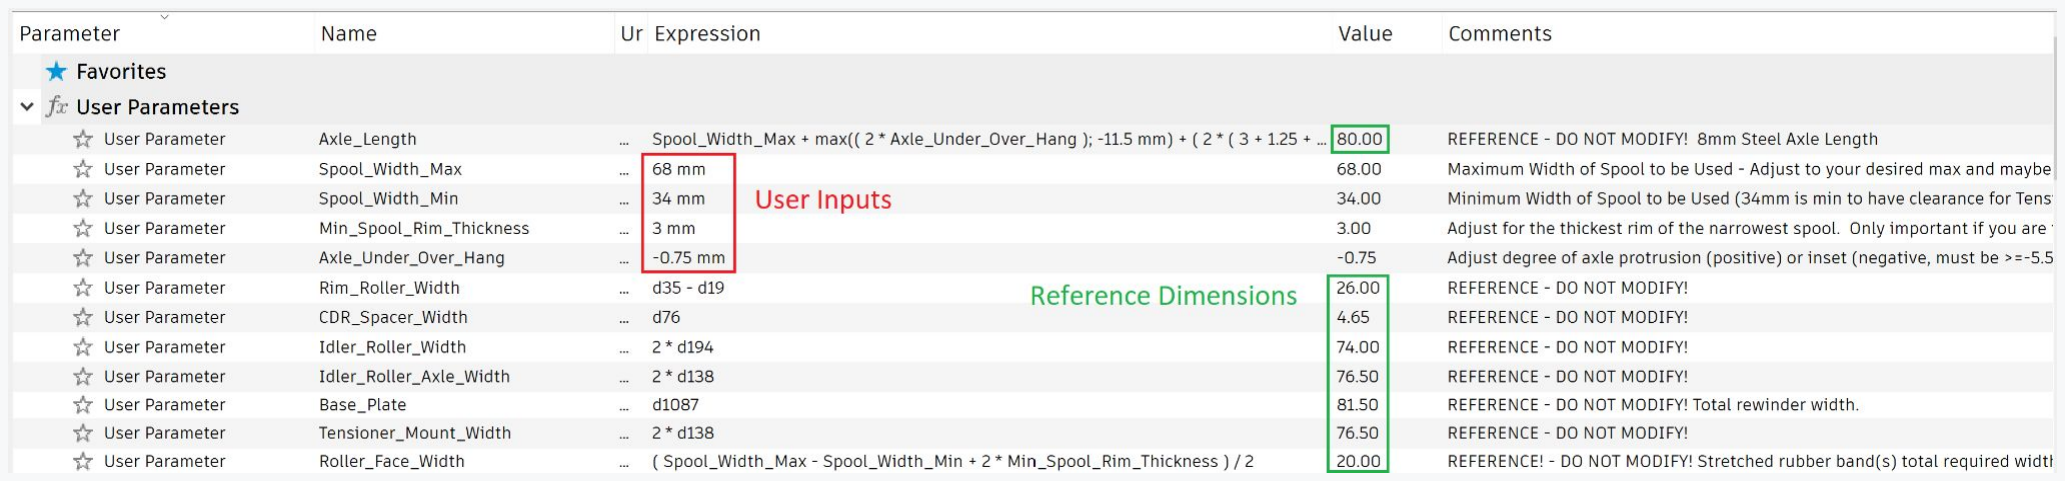
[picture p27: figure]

17 | 17

INTRODUCTION

THE PARAMETRIC CAD MODEL (continued)

Adjust the following parameters to meet your needs (continued from previous page):
Axle_Under_Over_Hang - This can be either a positive or negative number and is used to tweak the design to use a standard available axle length (like 80mm or 100mm). A negative number will result in the axle ends sitting inside the footprint of the rewinder but the model logic will not let you underhang more than 5.5mm inside the 608 bearing race to ensure good support of the axles from the bearings. A positive number will result in the axle protruding beyond the footprint of the rewinder. You may want to do this if you are going to use a readily available 100mm length axle but don't need a rewinder that can support spool widths as wide as 86mm, thus saving printing time and plastic by using a lesser Spool_Width_Max like 75mm. The best case scenario is to set this value at 0 and you have the ability to cut shaft stock to the exact length for your desired Spool_Width_Max (i.e. Spool_Width_Max = 75mm to accommodate virtually all 1KG spools and cut shaft to 88.5mm length).

Reference Parameters. DO NOT CHANGE THESE! These are included to assess the results of your inputs. You can iterate with changes to the User inputs to arrive at desired max spool width, standard axle widths, and/or readily available rubber band sizes.

The model will update to show the results of these parameters to help you visualize the acceptability of the result.

### OVERVIEW

## Idler Roller Assembly

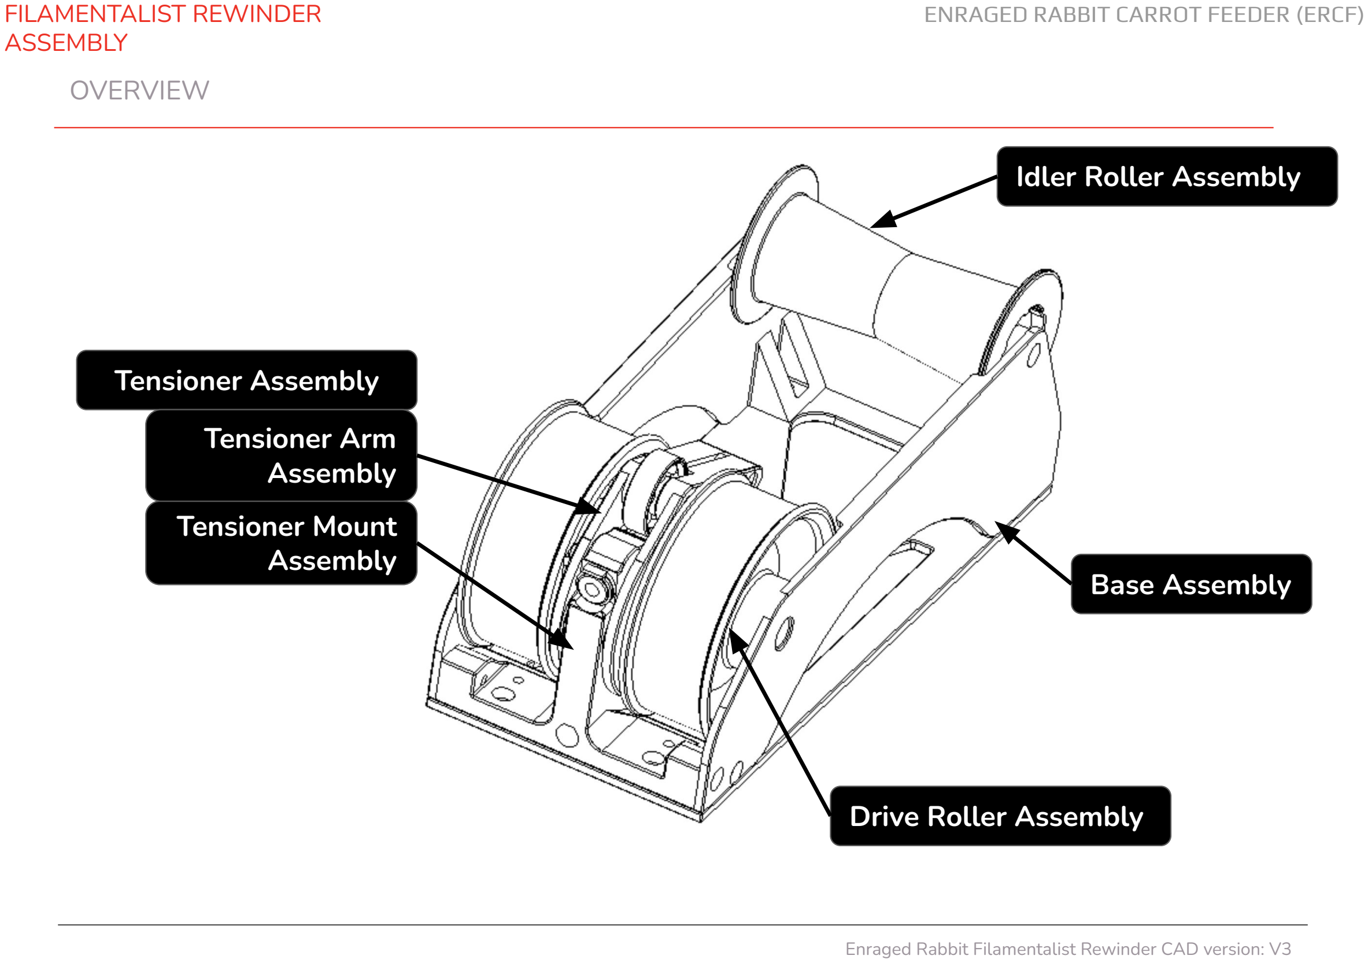
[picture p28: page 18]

ENRAGED RABBIT CARROT FEEDER (ERCF)

FILAMENTALIST REWINDER
ASSEMBLY

## Drive Roller Assembly

## Tensioner Assembly

## Base Assembly

## Tensioner Arm Assembly Tensioner Mount Assembly

ENRAGED RABBIT CARROT FEEDER (ERCF)

### DRIVE ROLLER ASSEMBLY

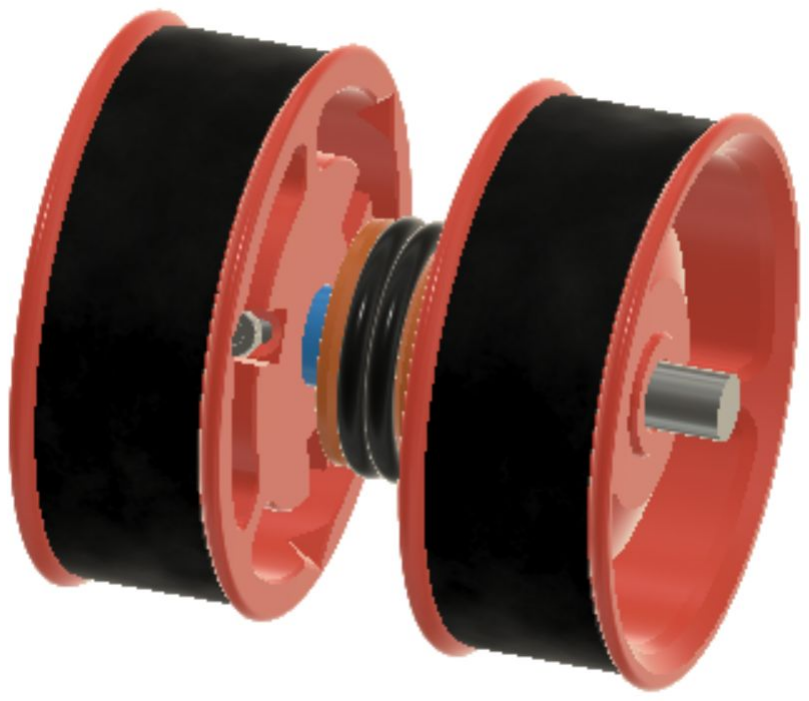
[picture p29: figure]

“You can’t have everything….where would you put it?” –Steven Wright

ENRAGED RABBIT CARROT FEEDER (ERCF)

### DRIVE ROLLER ASSEMBLY EXPLODED VIEW

DRIVE ROLLER ASSEMBLY BOM
(PER CHANNEL)

1x 8x80/100mm Stainless Steel Axle 2x AS568 Standard size 211 O-Ring 1x HF081412 One-Way Bearing 2-6x M3x8 Stainless SHCS Screw 2x Rubber Bands

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
2x [a]_Rim_Roller_80/100mm.stl 1x [a]_Center_Drive_Roller.stl
2x CDR_Spacer.stl
Axle_Depth_Tool.stl

DRIVE ROLLER ASSEMBLY PRINTED PARTS (PER CHANNEL)

A

B

C

F

H

G

D

### ASSEMBLY INSTRUCTIONS

1. Check the resistance of the one-way bearing on the axle. If the resistance is greater than the combined rolling resistance of the rest of the rewinder the one-way bearing will not disengage and freespool properly during filament loads resulting in loose coils on the spool. If you experience this issue please refer to the Filamentalist Troubleshooting Guide. (https://github.com/SkiBikePrint/Filamentalist/blob/main/troubleshoot.md)
2. Stretch O-Rings (part B) onto part G.
3. Press/tap part C into part G. This should be a tight fit. If too loose, use Super Glue or reprint with an increased extrusion factor. If too tight scrape the interior hole of Center Driver Roller with an Xacto knife. Orientation of the one-way bearing does not matter at this point.
4. Install screws into Rim Rollers to cut the threads (using a ball end hex driver makes this easier). Back the screws out a little to allow the axle to be inserted. If center bore of rollers is a close fit, only one screw per roller is required. If a loose fit, use 3 screws per roller to ensure roller is centered on Axle.

I

E

### DRIVE ROLLER ASSEMBLY (continued) EXPLODED VIEW

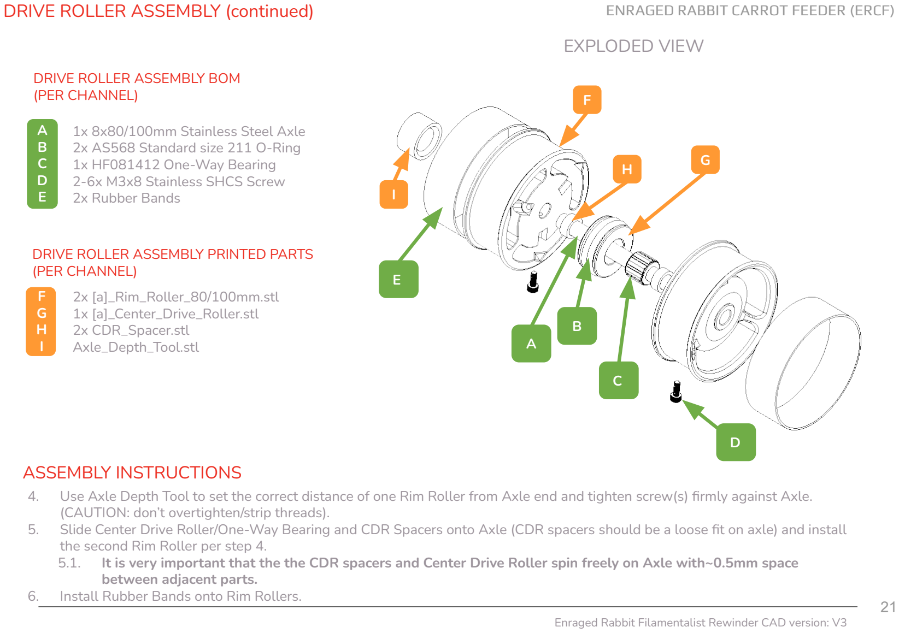
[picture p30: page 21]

ENRAGED RABBIT CARROT FEEDER (ERCF)

DRIVE ROLLER ASSEMBLY BOM
(PER CHANNEL)

1x 8x80/100mm Stainless Steel Axle 2x AS568 Standard size 211 O-Ring 1x HF081412 One-Way Bearing 2-6x M3x8 Stainless SHCS Screw 2x Rubber Bands

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
2x [a]_Rim_Roller_80/100mm.stl 1x [a]_Center_Drive_Roller.stl
2x CDR_Spacer.stl
Axle_Depth_Tool.stl

DRIVE ROLLER ASSEMBLY PRINTED PARTS (PER CHANNEL)

### ASSEMBLY INSTRUCTIONS

4. Use Axle Depth Tool to set the correct distance of one Rim Roller from Axle end and tighten screw(s) firmly against Axle. (CAUTION: don’t overtighten/strip threads).
5. Slide Center Drive Roller/One-Way Bearing and CDR Spacers onto Axle (CDR spacers should be a loose fit on axle) and install the second Rim Roller per step 4.
5.1. It is very important that the the CDR spacers and Center Drive Roller spin freely on Axle with~0.5mm space between adjacent parts.
6. Install Rubber Bands onto Rim Rollers.

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
ENRAGED RABBIT CARROT FEEDER (ERCF)

### IDLER ROLLER ASSEMBLY

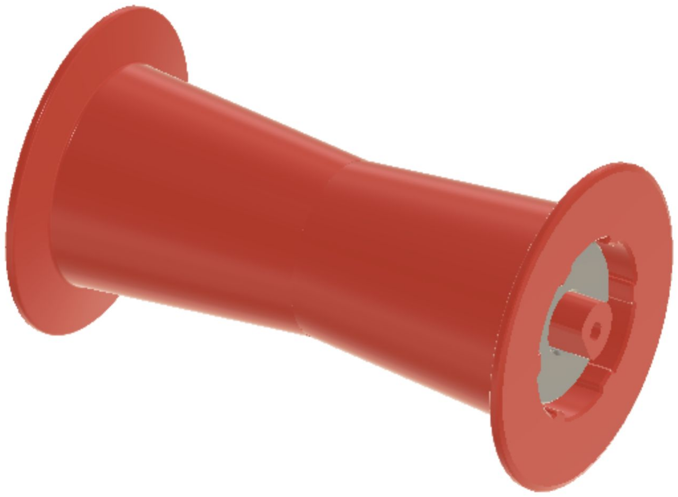
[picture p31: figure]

Q: What do you call a group of rabbits hopping backwards? A: A receding hare line

ENRAGED RABBIT CARROT FEEDER (ERCF)

### IDLER ROLLER ASSEMBLY

### EXPLODED VIEW

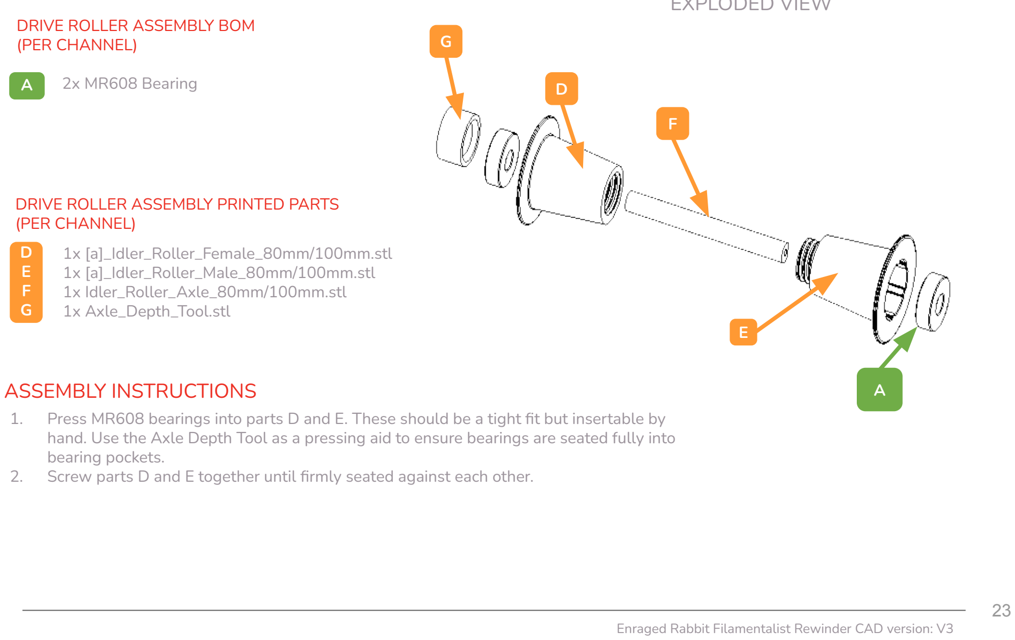
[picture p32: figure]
DRIVE ROLLER ASSEMBLY BOM (PER CHANNEL); A 2x MR608 Bearing; 1x [a]_Idler_Roller_Female_80mm/100mm.stl 1x [a]_Idler_Roller_Male_80mm/100mm.stl 1x Idler_Roller_Axle_80mm/100mm.stl 1x Axle_Depth_Tool.stl; DRIVE ROLLER ASSEMBLY PRINTED PARTS (PER CHANNEL); ASSEMBLY INSTRUCTIONS; bearing pockets.

1. Press MR608 bearings into parts D and E. These should be a tight fit but insertable by hand. Use the Axle Depth Tool as a pressing aid to ensure bearings are seated fully into
2. Screw parts D and E together until firmly seated against each other.

### TENSIONER MOUNT ASSEMBLY

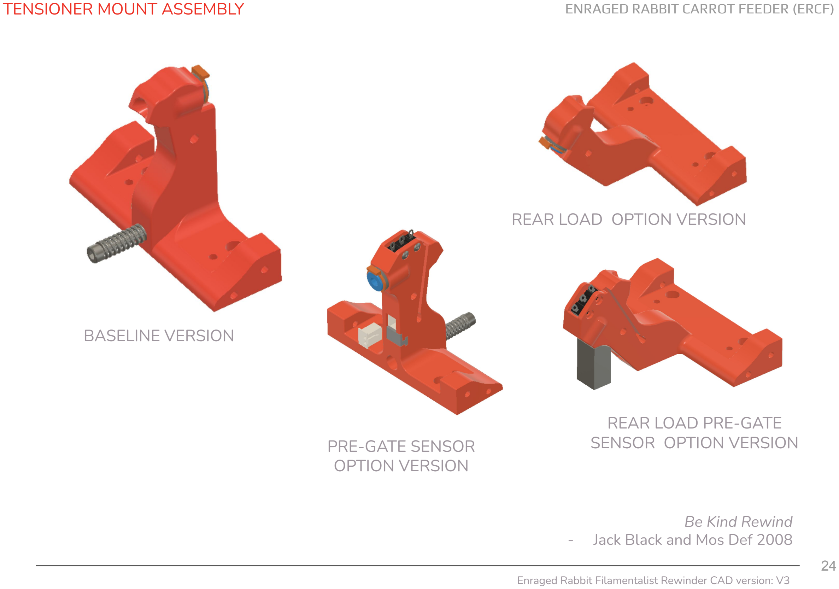
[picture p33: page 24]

ENRAGED RABBIT CARROT FEEDER (ERCF)

### BASELINE VERSION

### PRE-GATE SENSOR OPTION VERSION

### REAR LOAD PRE-GATE SENSOR OPTION VERSION

### REAR LOAD OPTION VERSION

Be Kind Rewind
- Jack Black and Mos Def 2008

ENRAGED RABBIT CARROT FEEDER (ERCF)

### TENSIONER MOUNT ASSEMBLY

TENSIONER MOUNT ASSEMBLY BOM (PER CHANNEL)
ECAS Fitting (remove rubber seal)
3mm Heatset Insert

A
B

F
G

1x [a]_Tensioner_Mount_80mm/100mm.stl
1x [a]_ECAS_Clip.stl (if not on-hand)

TENSIONER MOUNT ASSEMBLY PRINTED PARTS
(PER CHANNEL) | A

F

G

ALTERNATE/OPTIONAL PRINTED PART VERSIONS
(PER CHANNEL)
F 1x [a]_Tensioner_Mount_with_Sensor_80mm/100mm.stl
(split to parts in slicer for print-in-place breakaway connector retaining key) 1x [a]_Tensioner_Mount_Rear_Load_80mm/100mm.stl
1x [a]_Tensioner_Mount_Rear_Load_with_Sensor_80mm/100mm.stl

### EXPLODED VIEW

### ASSEMBLY INSTRUCTIONS

B

1. Install 3mm Heatset Insert.
2. Remove rubber seal and press ECAS Fitting into Tensioner Mount, ensuring it sits flush to face of hole. Using the 8mm axle as a pressing tool can help to get fitting fully inserted. Varying
ECAS and print tolerances could result in the ECAS hole cracking. If this happens, use superglue around the ECAS hole and crack(s).

Built-in
removable
support

PRE-GATE SENSOR
OPTION VERSION

REAR LOAD
OPTION VERSION

REAR LOAD
PRE-GATE SENSOR
OPTION VERSION

ENRAGED RABBIT CARROT FEEDER (ERCF)

### TENSIONER MOUNT ASSEMBLY (SENSOR OPTION)

SENSOR OPTION ADDITIONAL BOM ITEMS (PER CHANNEL)

1x D2F-L3 Microswitch
1x JST-XH 2-pin Socket
2x 60mm 24 AWG wire
2x M2x10 Self-tapping screw

A
B
C
D

F 1x [a]_Tensioner_Mount_with_Sensor_80mm/100mm.stl

TENSIONER MOUNT ASSEMBLY PRINTED PARTS
(PER CHANNEL)

A

B

B

F

ALTERNATE/OPTIONAL PRINTED PART VERSIONS
(PER CHANNEL)
F 1x [a]_Tensioner_Mount_Rear_Load_with_Sensor_80mm/100mm.stl

Built-in removable
support

### EXPLODED VIEW

### ASSEMBLY INSTRUCTIONS

1. Break away print-in-place JST-XH socket retaining clip using small flat blade screwdriver.
2. Install microswitch with 2x M2x10mm self tapping screws.
3. Strip 3mm from 24 AWG wire for JST-XH socket and tin with solder.
4. Feed wire through hole in wire slot and out opening for JST-XH socket.
5. Solder 2x wires at 90 degrees to terminals of JST-XH 2-pin socket and press socket into hole. Slide socket retaining clip back into place.
6. Press wire into slot and wrap around to the two switch terminals denoted with red dots in picture to assess length. Cut wire to length leaving 3mm for stripped ends to solder to terminals.
7. Solder wire to switch terminals.
8. Usa a 2-pin JST-XH plug for a harness running to main or MMU board.

BREAK
AWAY

C

D

ENRAGED RABBIT CARROT FEEDER (ERCF)

### TENSIONER ARM ASSEMBLY

TENSIONER ARM ASSEMBLY BOM (PER CHANNEL)

1x MR608 bearing
3x M3x16/18mm FHCS Screw
1x Spring
1x M3 Washer
1x M3x35mm +/- 10mm SHCS Screw

A
B
C
D
E

C
D

1x Tensioner_Arm_Left.stl
1x Tensioner_Arm_Rightstl

TENSIONER ARM ASSEMBLY PRINTED PARTS (PER CHANNEL)

A

B

C

D

Arm orientation for rear load version

| 1. Remove support from part D.

### EXPLODED VIEW

### ASSEMBLY INSTRUCTIONS

2. Lay part D on a flat surface. Slide the 608 bearing onto the bearing post.
Place part C into the 608 bearing and rotate against the part D making sure the
alignment tab seats correctly into the pocket at the bottom of part C.
3. Place a M3x12/16/18 FHCS screw through the bearing mount hole of part C and moderately tighten the screw into part D. Once installed verify that the bearing turns freely.
4. Place a M3x12/16/18 FHCS screw through the hole in part C at the "nose" end and moderately tighten the screw into part D.
5. Install the Tensioner Arm onto the Tensioner Mnt using a 3x16/18mm FHCS screw. Tighten until snug and then back off until the arm rotates freely on the mount.
6. Place an M3 washer followed by the spring onto an M3x25/35/45mm SHCS screw and slide through the slotted hole in the bottom of the Tensioner Arm Assembly. Screw the SHCS screw into the heatset insert of the Tensioner Mnt. No tension should be on the spring at this point.

Remove
Support
C

D

E

ENRAGED RABBIT CARROT FEEDER (ERCF)

### TENSIONER ARM ASSEMBLY

ALTERNATE TENSIONER SCREW ORIENTATION

### ASSEMBLY INSTRUCTIONS

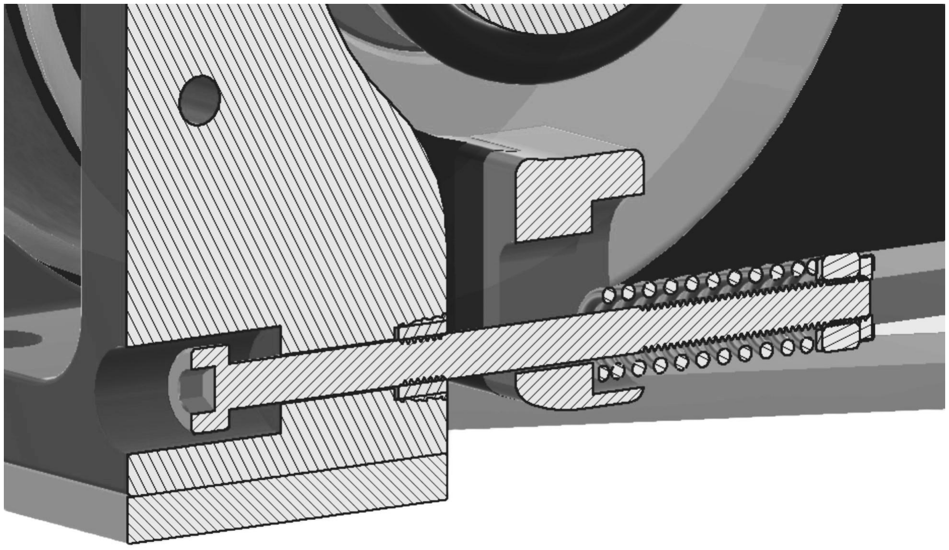
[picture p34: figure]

1. Insert the 3mm SHCS Tensioner screw from the bowden side of the rewinder through the heatset insert in the Tensioner Mount and the Tensioner Arm.
2. Insert the spring onto the Tensioner Screw.
3. Place an M3 washer followed by a lock nut, a nut with with threadlocker, or a heatset with threadlocker onto the Tensioner Screw to capture the spring.

If the orientation of your Filamentalist makes it difficult to access the tension adjustment screw you can reverse the 3mm SHCS Tensioner screw.

ENRAGED RABBIT CARROT FEEDER (ERCF)

### BASE ASSEMBLY

“Get back Jojo”
–The Beatles

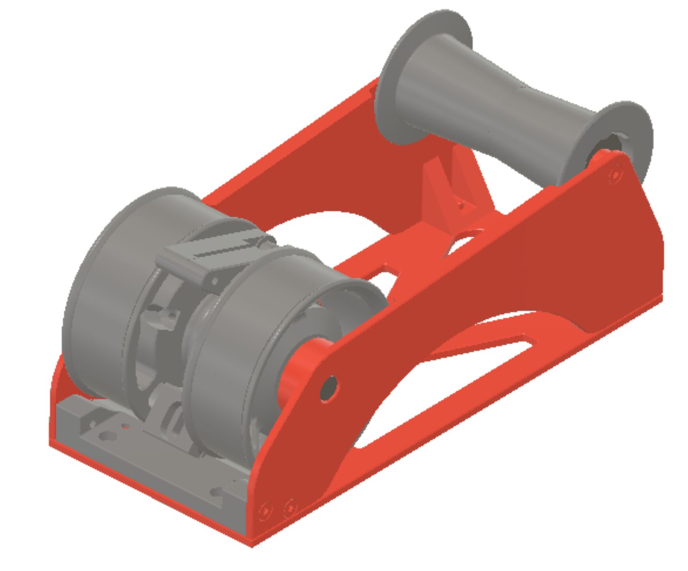
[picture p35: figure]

ENRAGED RABBIT CARROT FEEDER (ERCF)

### BASE ASSEMBLY

### EXPLODED VIEW

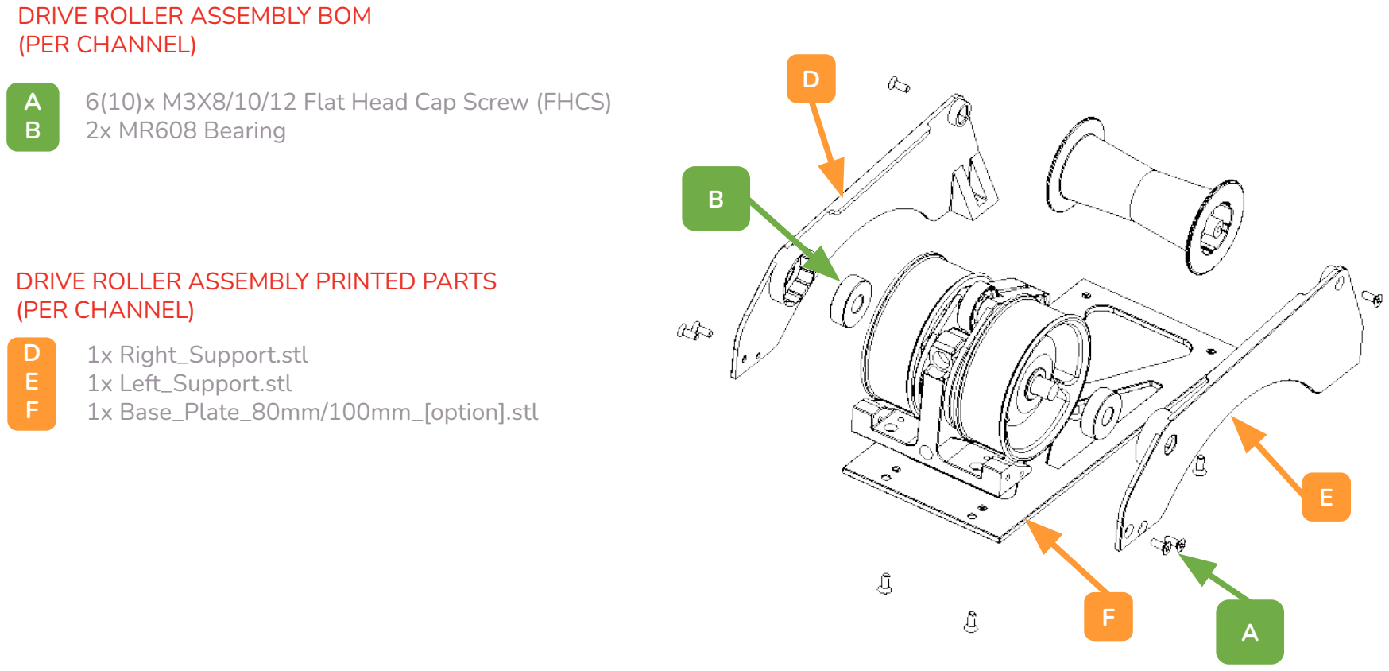
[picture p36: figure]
DRIVE ROLLER ASSEMBLY BOM (PER CHANNEL); 2x MR608 Bearing; 1x Right_Support.stl 1x Left_Support.stl 1x Base_Plate_80mm/100mm_[option].stl; DRIVE ROLLER ASSEMBLY PRINTED PARTS (PER CHANNEL)

6(10)x M3X8/10/12 Flat Head Cap Screw (FHCS)

ENRAGED RABBIT CARROT FEEDER (ERCF)

### BASE ASSEMBLY

### EXPLODED VIEW

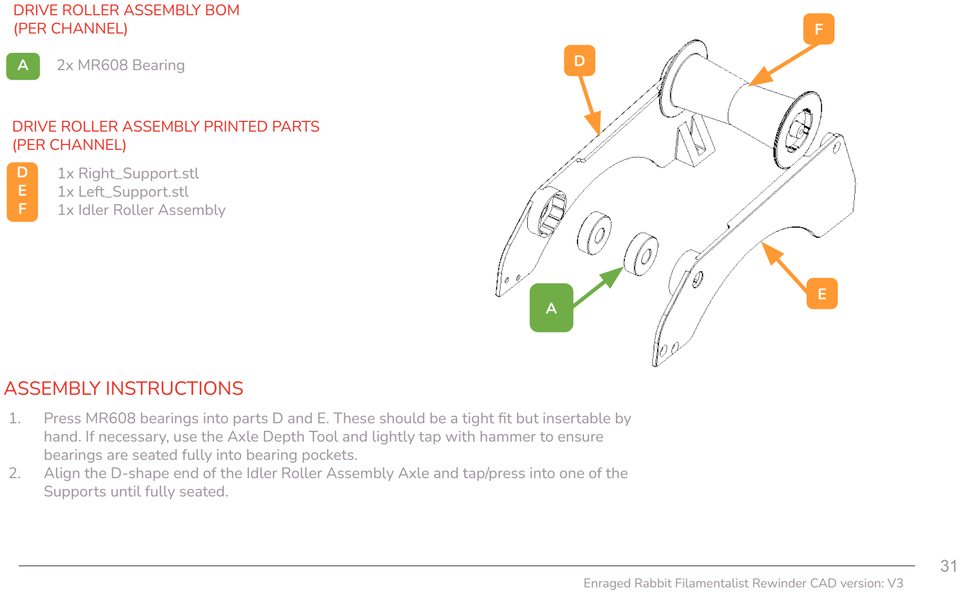
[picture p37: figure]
DRIVE ROLLER ASSEMBLY BOM (PER CHANNEL); 2x MR608 Bearing; 1x Right_Support.stl 1x Left_Support.stl 1x Idler Roller Assembly; DRIVE ROLLER ASSEMBLY PRINTED PARTS (PER CHANNEL); ASSEMBLY INSTRUCTIONS; Supports until fully seated.

1. Press MR608 bearings into parts D and E. These should be a tight fit but insertable by hand. If necessary, use the Axle Depth Tool and lightly tap with hammer to ensure bearings are seated fully into bearing pockets.
2. Align the D-shape end of the Idler Roller Assembly Axle and tap/press into one of the

ENRAGED RABBIT CARROT FEEDER (ERCF)

### BASE ASSEMBLY (continued)

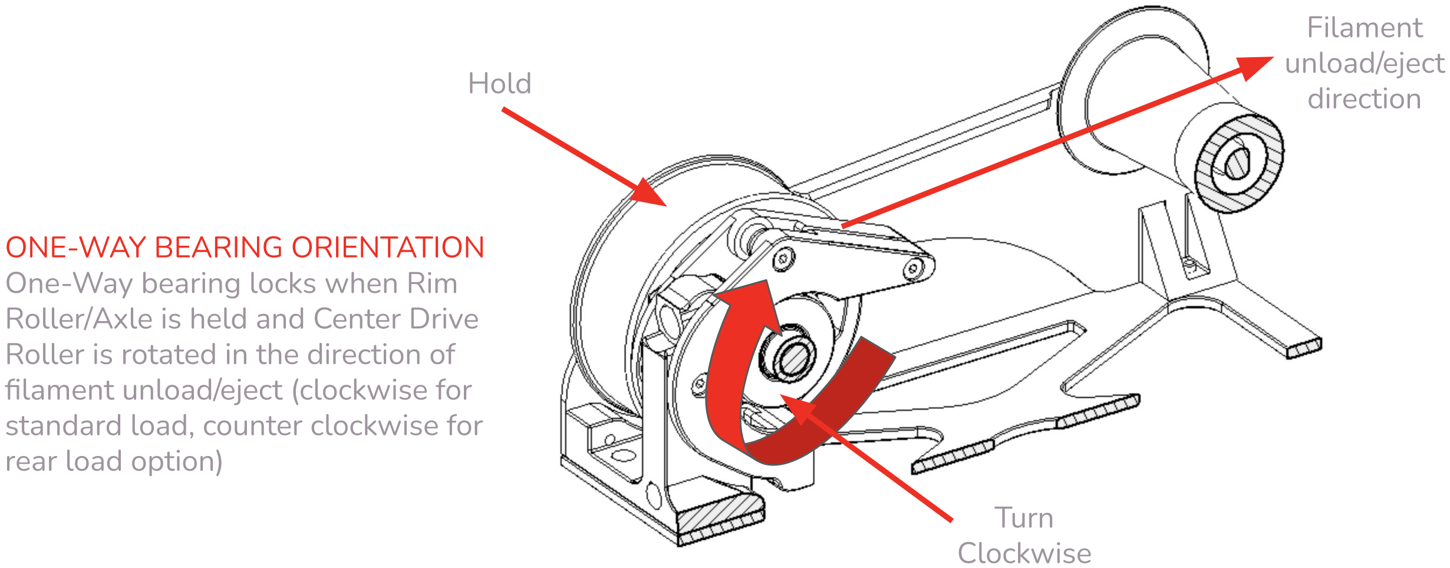
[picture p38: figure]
ONE-WAY BEARING ORIENTATION One-Way bearing locks when Rim Roller/Axle is held and Center Drive Roller is rotated in the direction of filament unload/eject (clockwise for standard load, counter clockwise for rear load option); Filament unload/eject direction Hold; Turn Clockwise

### ASSEMBLY INSTRUCTIONS (continued)

3. Insert Drive Roller Assembly axle into the MR608 bearing of the Support that has the Idler Roller Assembly installed on it.
3.1. IMPORTANT! Orient the Drive Roller Assembly so that the one-way bearing of the Center Drive Roller locks when rotated in the direction of a filament unload (if using the Tensioner Mount Rear Load option then the one-way bearing must be reversed and operate/lock in the counterclockwise direction with respect to the picture above).
4. Place Tensioner Assembly onto/over Drive Roller Assembly and Idler Roller onto Idler Roller Axle.

### BASE ASSEMBLY (continued)

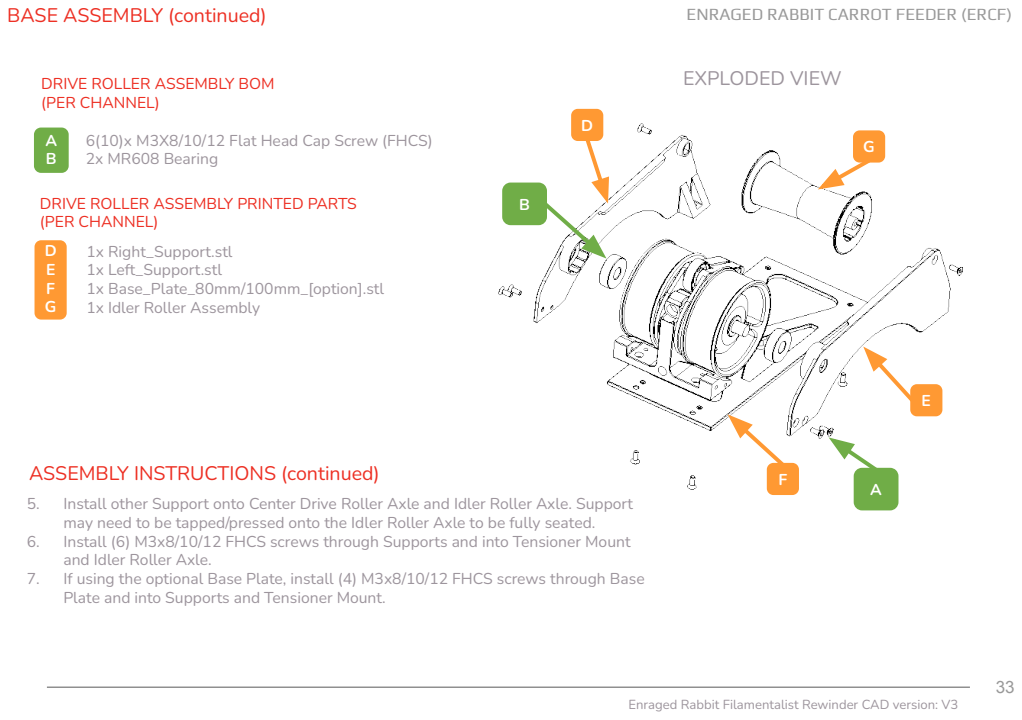
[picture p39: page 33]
DRIVE ROLLER ASSEMBLY BOM; EXPLODED VIEW; 1x Right_Support.stl 1x Left_Support.stl 1x Base_Plate_80mm/100mm_[option].stl 1x Idler Roller Assembly; DRIVE ROLLER ASSEMBLY PRINTED PARTS (PER CHANNEL)

ENRAGED RABBIT CARROT FEEDER (ERCF)

(PER CHANNEL)
6(10)x M3X8/10/12 Flat Head Cap Screw (FHCS)
2x MR608 Bearing

ASSEMBLY INSTRUCTIONS (continued)
5. Install other Support onto Center Drive Roller Axle and Idler Roller Axle. Support
may need to be tapped/pressed onto the Idler Roller Axle to be fully seated.
6. Install (6) M3x8/10/12 FHCS screws through Supports and into Tensioner Mount
and Idler Roller Axle.
7. If using the optional Base Plate, install (4) M3x8/10/12 FHCS screws through Base
Plate and into Supports and Tensioner Mount.

ENRAGED RABBIT CARROT FEEDER (ERCF)

### BASE ASSEMBLY (continued)

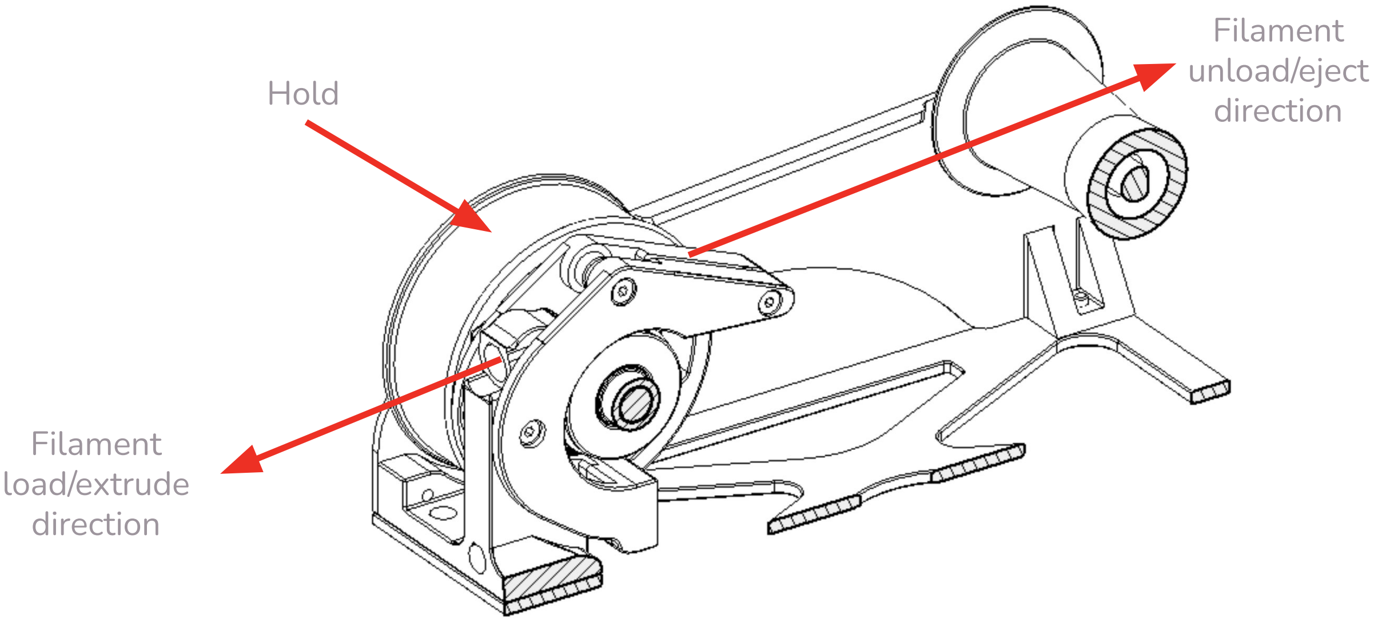
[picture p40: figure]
Filament unload/eject direction Hold; Filament load/extrude direction

8. Verify again that One-Way bearing is installed correctly. Insert a piece of filament through the filament path and tighten the Tensioner Screw to create medium spring tension.
9. Hold the center roller by placing your thumb/finger against the o-rings and try to pull the filament out in the eject direction.
10. The slip force/resistance against the filament should “light-to-moderate” (~0.2-0.3 kg or ~7-10 oz). Adjust the spring tensioner screw accordingly and err on the light side for a starting point.
11. While holding a Rim Roller with one hand, move the filament in the eject direction (see picture above). The Rim Roller should try to rotate against the pressure of your hand.
12. Continuing to hold a Rim Roller, move the filament in the load/extrude direction. The Rim Roller should not try to move and the Center Drive Roller should turn freely.

### ASSEMBLY INSTRUCTIONS (continued)

ENRAGED RABBIT CARROT FEEDER (ERCF)

### TUNING

### TUNING INSTRUCTIONS

Tune by setting the Tensioner Arm clamping force. The arm does not need an extreme amount of tension.
1. As a bench test (not connected to the MMU yet), load a spool of filament onto the rewinder and insert the filament through the o-ring/bearing interface and out the ECAS side of the Tensioner Mount.
1.1. IMPORTANT! The filament should feed through the slot in the “nose” of the Tensioner Arm.
2. Hold the center roller by placing your thumb/finger against the o-rings and try to pull the filament out in the eject direction.
3. The slip force/resistance should “light-to-moderate” (~0.2-0.3 kg or ~7-10 oz). Adjust the spring tensioner screw accordingly and err on the light side for a starting point.
4. Pull ~1m of filament in the load direction. Filament should stay tight on the spool (no loose loops). If loose loops form this indicates that the One-Way Bearing/Center Drive Assembly may be installed backwards (return to Center Drive Roller Assembly step), or the One-Way bearing is too tight on the Center Drive Roller Axle (see Filamentalist Troubleshooting Guide.). (https://github.com/SkiBikePrint/Filamentalist/blob/main/troubleshoot.md)
5. Starting with a tightly packed filament roll, push filament back onto the spool to simulate an MMU unload/eject. If loose filament is forming around the filament spool during unload, tighten the spring tensioning screw. If no loose filament is forming around the filament roll, gradually reduce the spring tension until loose filament starts to accumulate and then increase tension in ~1/2 screw turn increments until you feel you have the lightest tension that results in a tightly packed unload.
6. Initial tuning is complete and the rewinder can now be installed into your system. The same steps above can be followed after rewinder installation if additional tuning is required.

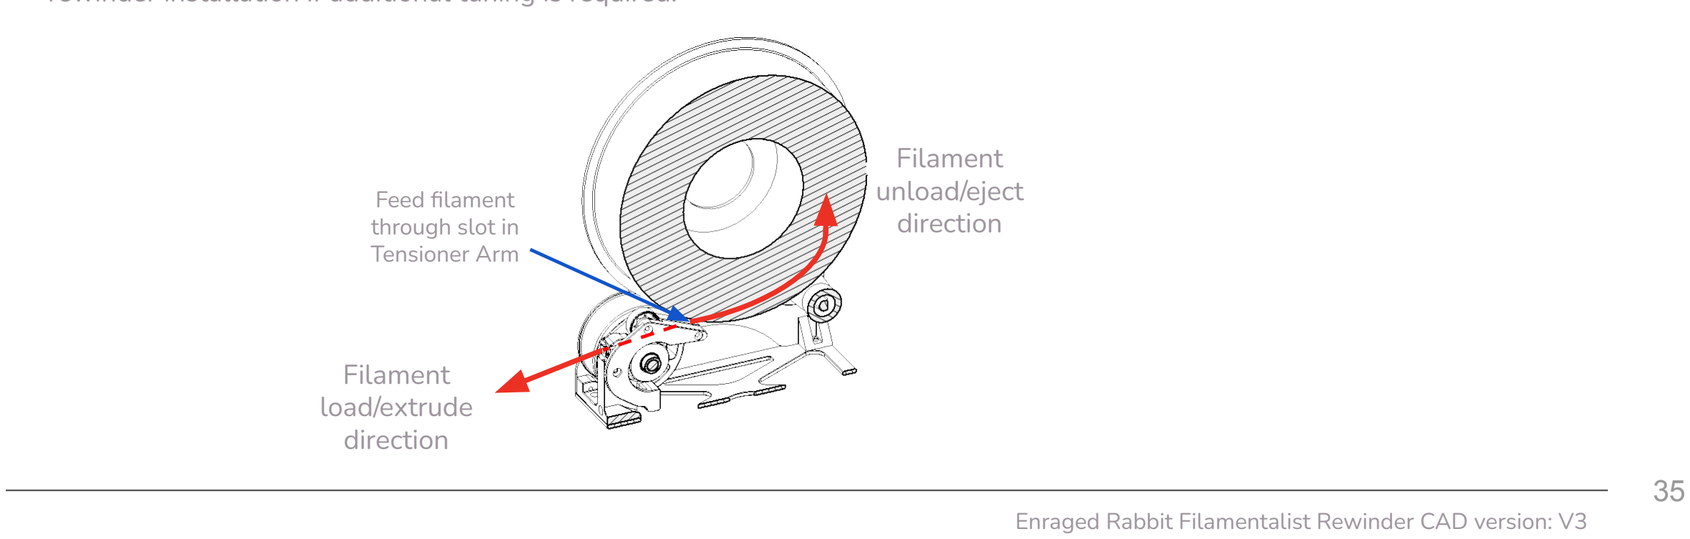
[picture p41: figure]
Filament unload/eject direction; Filament load/extrude direction; Feed filament through slot in Tensioner Arm

ENRAGED RABBIT CARROT FEEDER (ERCF)

### O-RING REPLACEMENT

You may never need to replace o-rings. Testing and extrapolation estimates that the wear-out point is ~5K cycles. The impact of o-ring wear-out can be reduced by periodically swapping highly used rewinders with low use rewinders in your line-up. Also, o-rings with grooves worn in them can be swapped with their opposing partners to present the unworn side/face to the filament to extend the life of a set. For o-ring replacement, FOLLOW THE STEPS BELOW:

1. Unscrew the (6) screws of the Right and Left Supports and remove them.
2. Remove the Drive Roller Assembly from under the Tension Mount Arms.
3. Unscrew the set screw(s) on one Rim Roller and remove it from the axle.
4. Slide the CDR Spacer and Center Drive Roller from the axle
5. Remove the old o-rings (a dental pic or small flat bladed screwdriver works great).
6. Install a pair of new o-rings.
7. Reinstall the Center Drive Roller and CDR Spacer back on the axle.
8. Install the Rim Roller back onto the axle.
a. Use Axle Depth Tool to set the correct distance of Rim Rollers from Axle end and tighten screw(s) firmly against Axle.
b. Confirm that the CDR spacers still freely spin on Axle with~0.5mm space between adjacent parts.
9. Verify that the Center Drive Roller Assembly/One-Way Bearing is in the correct orientation and reassembly the unit.

ENRAGED RABBIT CARROT FEEDER (ERCF)

### Questions, Troubleshooting, and Help

1. If your rewinder is not functioning properly please reference the Troubleshooting guide on Github here: https://github.com/Enraged-Rabbit-Community/ERCF_v2/blob/b06b4bec456481a31ca77793b5a11747fa6342c3/Recommended_Options/Filamentalist_Rewinder/troubleshoot.md (https://github.com/Enraged-Rabbit-Community/ERCF_v2/blob/b06b4bec456481a31ca77793b5a11747fa6342c3/Recommended_Options/Filamentalist_Rewinder/troubleshoot.md)
a. A video demonstrating the heat rework procedure for tight one-way bearings can be found at 4:20 in the Assembly Video here: https://youtu.be/-1cHOcnosxE
2. Common questions are answered in the FAQ on Github here: https://github.com/Enraged-Rabbit-Community/ERCF_v2/blob/b06b4bec456481a31ca77793b5a11747fa6342c3/Recommended_Options/Filamentalist_Rewinder/Filamentalist_FAQ.md
3. There is an active community supporting and improving the Filamentalist rewinder on Discord here:
https://discord.gg/hxe9eMWseT

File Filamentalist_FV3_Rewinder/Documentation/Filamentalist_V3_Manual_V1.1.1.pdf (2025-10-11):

# ERCF

### User Community Help on Discord Here! (https://youtu.be/5Qk3N2sKz40)

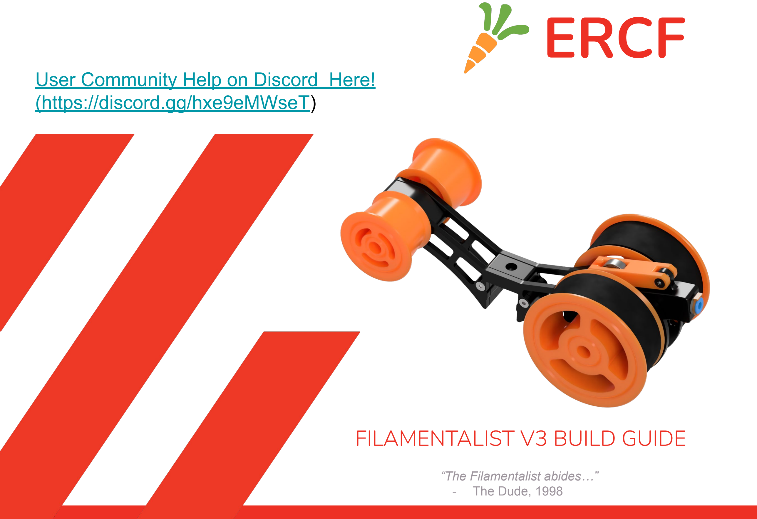
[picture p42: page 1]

# FILAMENTALIST V3 BUILD GUIDE

“The Filamentalist abides…”
- The Dude, 1998

### (https://discord.gg/hxe9eMWseT)

ENRAGED RABBIT CARROT FEEDER (ERCF)

Filamentalist Rewinder V3 CAD version: V1 2 | 2

FILAMENTALIST V3

Introduction
Theory of Operation | 3
Acknowledgements | 4
Configuration/Options | 5
Part Printing Guidelines | 7
STL File Naming Key | 9
Hardware Reference | 10
Required Tools | 11
CAD Files and Parametric Model | 13
Assembly | 16
Tensioner Arm | 17
Tensioner Mount | 18

## TABLE OF CONTENTS

Assembly (cont.)

Center Drive Roller (CDR) | 20
Chassis | 21
CDR/Tensioner Arm | 25
One-Way Bearing Orientation | 26
Rim/Idler Rollers | 27
Tuning | 28
O-Ring Replacement | 29
Questions, Troubleshooting, and Help | 30

Be Kind Rewind
–2008 starring Jack Black and Mos Def

ENRAGED RABBIT CARROT FEEDER (ERCF)

Filamentalist Rewinder V3 CAD version: V1

### INTRODUCTION

The Filamentalist is an integrated solution for buffering and spool holding, providing space savings as well as the potential for filament path reduction, and the associated drag/resistance that comes with long runs from spool to buffer to MMU.
- The Filamentalist uses the axial force delivered by the MMU gear motor along the filament to load and unload from the filament spool.
- An adjustable spring clamp forces the filament against two o-rings that sit on the Center Drive Roller (CDR) to create a high traction interface, for rotating the axle and filament spool.
- A one-way clutch style bearing locks against the Drive Axle and rotates the filament spool, to take up filament during an unload.
- For loading and print extruding, the clutch disengages allowing for effective free-spooling of the filament spool similar to a roller style spool holder.
- The difference in diameter of the filament driven CDR versus the larger Rim Roller that the filament spool sits on provides the needed gear ratio to produce enough rotations to take up, and unload a nearly empty or full filament roll.
- During unloading/buffering, to account for the varying diameter of a spool from full to empty, filament tension will cause the spring loaded arm to lift a small amount and release traction from the o-rings allowing slip to occur between the filament and the o-ring interface of the rewinder (full spool = max slip, empty spool = no/minimal slip). This grip/slip modulation effectively creates a variable gear ratio allowing for clean, tight wraps during unload with a minimum of system drag.

THEORY OF OPERATION

ONE-WAY BEARING

O-RING/FILAMENT
INTERFACE

GEAR RATIO FOR
EMPTY-TO-FULL
SPOOL RANGE

DRIVE AXLE

SPRING TENSION

ENRAGED RABBIT CARROT FEEDER (ERCF)

### INTRODUCTION

I would like to acknowledgement and thank:
thisiscam (on Discord) who shared Muzi Xiaoyang's video of a filament driven rewinder and then continued to partner and share his brilliance in the evolution and optimization of the final product.

The original Beta Test Team (on Discord) who provided design validation and innumerous inputs for design improvements, printability, and simplification of assembly.
Cheesefrog
Grafton
Biokeks
Meltiseugen
JCPhlux
and many more…

All the Early Adopters who allowed a fleet of hundreds of rewinders to help further refine the Filamentalist, the documentation, and volume unit validation. You know who you are!
v6cl (on Discord) for his innovative F1 User Mod that was a core input to the Filamentalist V3 design.
JCPhlux for suggesting the printed clutch design
The ERCF Team for building, supporting, and allowing me to be part of this amazing ecosystem of multi-material printing solutions! Your creativity, commitment, professionalism, collaboration, generosity, and sense of community is an inspiration!

ACKNOWLEDGEMENTS

ENRAGED RABBIT CARROT FEEDER (ERCF)

Filamentalist Rewinder V3 CAD version: V1 5

Things that you need to know include:

There are multiple options for the Filamentalist. Determine which versions/options you want and select the stl's to print accordingly.

- Unit Width: Standard width which supports spool widths from 28mm (i.e. 200gm spools) to 74mm and custom width via the Fusion 360 parametric model
- Drive and Idler Axle bearing size. Step and STL files are provided for the use of either 688 bearings (16mm OD X 8mm ID X 5mm width) or 608 bearings (22mm OD X 8mm ID X 7mm width). Either option can be selected in the provided Fusion 360 parametric model.
- Mounting Style: 2020 center rail mount, 2020 dual rail mount (fits the Filamentalist Enclosure), and Standalone mount

Feed Direction: The orientation of your MMU with respect to your filament spools location or enclosure may require a front, rear, or bottom loading capability from the rewinder. Front and Rear/Bottom feed Tensioner Mount options are provided to support this.

Pre-gate Sensors: If your MMU does not have pre-gate sensors, and the software you use supports them (like Happy Hare), there are CottonTail Lite, Filamentalist Tensioner Mount, and user mod pre-gate sensors that support this. (see the Filamentalist FAQ).

If you are using, or upgrading from an ERCFv1 or v2 version you may want/need a higher torque gear motor. Many in the Beta team ran NEMA 17's spec'd at 55 N-cm max torque and config'd them for 1-1.5A (probably overkill...). A NEMA 17 with 40N-cm or greater holding torque is sufficient. The LDO-42STH47-1684AC stepper is a good option. The ERCF direct drive version is recommended for gaining more speed from a high torque motor. This may not be required, so if you already have built your ERCF, try the Filamentalist with the motor/gearing you have and decide if you need more torque/speed.

INTRODUCTION

CONFIGURATION/OPTIONS CONSIDERATIONS

ENRAGED RABBIT CARROT FEEDER (ERCF)

The standard width Filamentalist has a 50-75mm axle and supports a maximum spool width of 74mm and supports most standard 1, 0.5, and 0.2KG spool sizes and still be able to fit 6 rewinders across the top of a 350 size Voron printer. If you use spools wider than 74mm and you use Autodesk Fusion 360, the provided .f3d file in the CAD directory is a parametric based model allowing you to customize the width of your rewinder to suit your max/min spool widths and/or to design around other available 8mm steel axle lengths (see Parametric CAD Model section in this document). If you are unable to use the parametric model please ask for help on Discord (see cover page and/or page 31 for links).

Because the standard tuning of this design relies on some filament slip at the o-rings, the o-rings may ultimately wear-out. Testing and extrapolation estimates that the wear-out point is greater than 5K cycles. See the O-Ring Replacement section at the end of this document for o-ring swap/replacement instructions.

Enjoy the process of building and utilizing your Filamentalist Rewinder!

INTRODUCTION

CONFIGURATION/OPTIONS CONSIDERATIONS (continued)

ENRAGED RABBIT CARROT FEEDER (ERCF)

The ERCF team has provided the following print guidelines. We recommend you to follow them in order to have the best chance at success with your parts. There are often questions about substituting materials or changing printing standards, but we recommend you follow these.

The majority of mechanical issues users experience with the ERCF and its supporting components can be traced back to print quality and and accuracy. Please take the time to print the calibration tools and dial in your printer before moving forward.

INTRODUCTION

FDM MATERIAL
The Filamentalist was designed for, and
tested with ABS and ASA. Based on the tolerance requirements of the design we recommend to only use ABS OR ASA. Some users have built with other materials such as PLA but you may need to adjust your printer’s calibration for some press-fit and tight tolerance parts.

LAYER HEIGHT
Recommended : 0.2mm
First Layer: 0.25mm

INFILL PERCENTAGE
Recommended: 40%

EXTRUSION WIDTH
Recommended : Forced 0.4mm

WALL COUNT
Recommended : 4

INFILL TYPE
Grid, Gyroid, Honeycomb, Triangle or Cubic.

SOLID TOP/BOTTOM LAYERS
Recommended : 5

### PART PRINTING GUIDELINES

ENRAGED RABBIT CARROT FEEDER (ERCF)

IMPORTANT !! The Filamentalist design relies on multiple press-fits for bearings, axle, and the ECAS04 fitting as well as thread-cut holes. As a result, printer calibration is important. The Print_Calibration_Tool.stl is included. It is highly recommended that you print this block first, check fits, and make adjustments to extrusion multipliers and/or slicer scaling if needed before printing the Filamentalist parts.

INTRODUCTION

### THE PRINT CALIBRATION TOOL

Print_Calibration_Tool.stl

M3 Thread Cutting Hole

ECAS04 Hole
(tight press fit)

TESTS
Insert the different pieces of hardware in their dedicated positions.

The ECAS fitting should be a tight press fit. If the plastic cracks after ECAS insertion or the ECAS is a loose fit then extrusion rates and/or interior hole settings need to be adjusted in your slicer. You may need to cut the print with clippers to remove the ECAS for reuse after checking fit.

You should be able to hand press in a 688/608 bearing into the pocket. It is acceptable if additional force, like light hammer taps is required to fully seat the bearing. The bearing can be removed by inserting an 8mm axle/rod through the bearing and rocking the rod back and forth while gently pulling on the rod, “walking” the bearing out of the pocket.

Screw an M3 screw into the provided 2.7mm diameter hole. The screw should tightly screw in and cut threads into the plastic. If the ECAS and 688/608 bearing press in nicely but this hole is tight, no print adjustments need to be made but M3 screw holes may need to be opened up hand twisting a 2.5mm drill bit.

688/608 Bearing Hole
(easy press fit)

M3 Clearance Hole

8mm Axle Hole
(easy press fit)

ENRAGED RABBIT CARROT FEEDER (ERCF)

FILE NAMING
By this time you should have already downloaded our STL files from the ERCF GitHub. This is how to use the naming conventions.

[a]_Part_Name_{Bearing_Size}_{Quantity_Required}_[option].stl

Example [a]_Rim_Roller_688_Bearing_x2.stl

INTRODUCTION

PRIMARY COLOR
Example
Tensioner_Mount_Std.stl
These files will have nothing at the start of the filename.

ACCENT COLOR
Example
[a]_Tensioner_Arm.stl
These files have an ‘’[a]_’’ prefix to denote that they should be printed with an
accent color.

BEARING SIZE
Filenames with an
‘’688_Bearing’’ or
“608_Bearing” after the file name are specific to the
bearing size option you choose to build.

QUANTITY REQUIRED
Filenames ending with ‘’_x#’’ are telling you the quantity of that part required to build a single rewinder

STL FILE NAMING KEY

[option]
Filenames with an “[option]” after the filename are build options/alternatives such as:
- Mount style
- Pre-gate sensor included in Tensioner Mount
- Printed clutch vs One-Way bearing

ENRAGED RABBIT CARROT FEEDER (ERCF)

INTRODUCTION

FLAT HEAD COUNTERSUNK SCREW (FHCS)
Metric fastener with a cone shaped head and a flat top.

ISO 10642

SOCKET HEAD CAP SCREW (SHCS) Metric fastener with a cylindrical head and hex drive. The most common fastener used on the ERCF.

ISO 4762


WASHER
Plain metal stamped washer.

DIN 125

688/608 BEARING
For the Filamentalist, the 2RS (sealed) style is preferred but can be used with the open or ZZ (shielded) style.


HEAT SET INSERT
Brass, threaded, with ridges on the outside. Heat to approx 250C with soldering iron and push into a hole in the plastic. Plastic cools and solidifies around the knurls/ridges for excellent resistance to torque and pull-out.

SPRING
For the Filamentalist, 304 Stainless Steel,6mm OD, 0.6mm Wire Size, 15mm Free Length spring used in Tensioner Assembly.

ECAS FITTING
4mm Push -Fit PTFE tubing fitting.

HARDWARE REFERENCE

ENRAGED RABBIT CARROT FEEDER (ERCF)

INTRODUCTION


2.5MM HEX DRIVER
Adjustment of the Tensioner screw in this design benefits from the use of a 2.5mm hex driver. The ball-end style is preferred. This driver is also used for the axle set screws on the Rim Rollers.

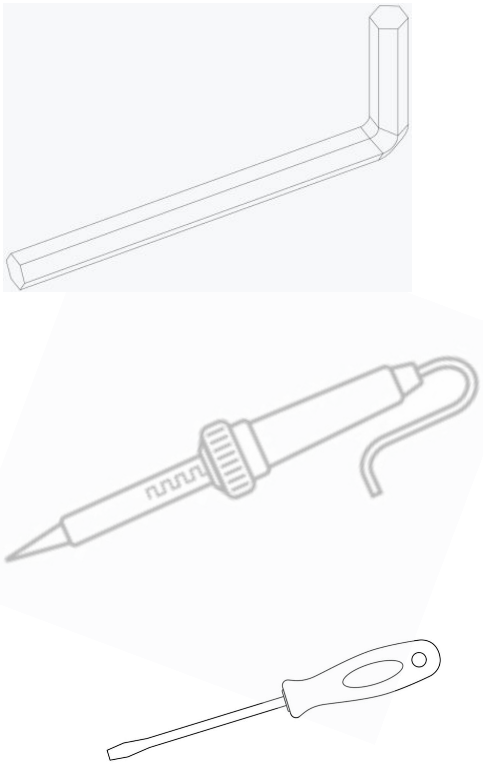
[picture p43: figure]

2MM HEX DRIVER
The 2mm hex driver is used on the M3 FHCS screws in this build.

SOLDERING IRON
For the insertion of the single heat set insert in the Tensioner Mount part.

TOOLS

SMALL FLAT BLADED SCREWDRIVER To aid in the removal of built-in supports.

ENRAGED RABBIT CARROT FEEDER (ERCF)

INTRODUCTION | TOOLS

ANGLE GRINDER/DREMEL
For cutting 8mm axle rods/tubes to length if
required.
VISE
A vise is handy cutting 8mm axles and pressing the one-way bearing into the CDR.
CAD SOFTWARE
Filamentalist_V3_688/608_bearing.step or Filamentalist_V3_(parametric).f3d
Software is a tool too! The CAD file for the Filamentalist was designed to be used along with this manual as a supplement or reference, even if you aren’t a CAD Pro. You can use the free edition of Fusion360, or your choice of CAD program such as TinkerCAD, onshape, or FreeCAD.
SUPERGLUE
Yes, we consider this a tool. Superglue may be useful if your print tolerances result in slip-fits for the bearings and ECAS. Cheap, single-use gel tubes are fine.

PRINT CALIBRATION TOOL
https://github.com/Enraged-Rabbit-Community/ERCF_v2/tree/master/Recommended_Options/Filamentalist_Rewinder/Filamentalist_FV3/Stls/Tools (https://github.com/Enraged-Rabbit-Community/ERCF_v2/tree/master/Recommended_Options/Filamentalist_Rewinder/Filamentalist_FV3/Stls/Tools) It is highly recommended that you print this Print_Calibration_Tool.stl part first, check fits of M3 screws (both slip fit and thread cutting), 608/688 bearings, 8mm axle lightpress/slip fit, and the ECAS04 press fit. Make adjustments to extrusion multipliers and/or slicer scaling if needed before printing the Filamentalist parts.

ENRAGED RABBIT CARROT FEEDER (ERCF)

We have provided the Filamentalist CAD files (https://github.com/Enraged-Rabbit-Community/ERCF_v2/tree/master/Recommended_Options/Filamentalist_Rewinder/Filamentalist_FV3_beta/CAD/Filamentalist_V3_beta_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 and Filamentalist_V3_beta_(parametric)_V##.f3d), so that you can follow along with the instructions in a 3D view, if you like.

The CAD file is organized into folders based on assemblies referenced in this manual. First hide all the parts, and then reveal the parts up to the step you are on in this manual, and the CAD should match what you are building.

All of the non-printed parts are in each assembly’s Hardware folder.

INTRODUCTION

USING THE CAD FILES

ENRAGED RABBIT CARROT FEEDER (ERCF)

If you are using Autodesk Fusion 360 the “Filamentalist_V3_(parametric).f3d file provided in the CAD folder is a parametric based model allowing you to customize the width of your rewinder to suit your max/min spool widths and/or to design around a standard available steel axle length. The model will update and accurately show the results of these parameters to help you visualize the acceptability of the result as well as provide reference dimensions to aid in part sourcing.
To customize your Filamentalist width and axle sizing, load the model, make sure you are in the "Solid" menu, and then select "Modify" and "Change Parameters"

INTRODUCTION

THE PARAMETRIC CAD MODEL

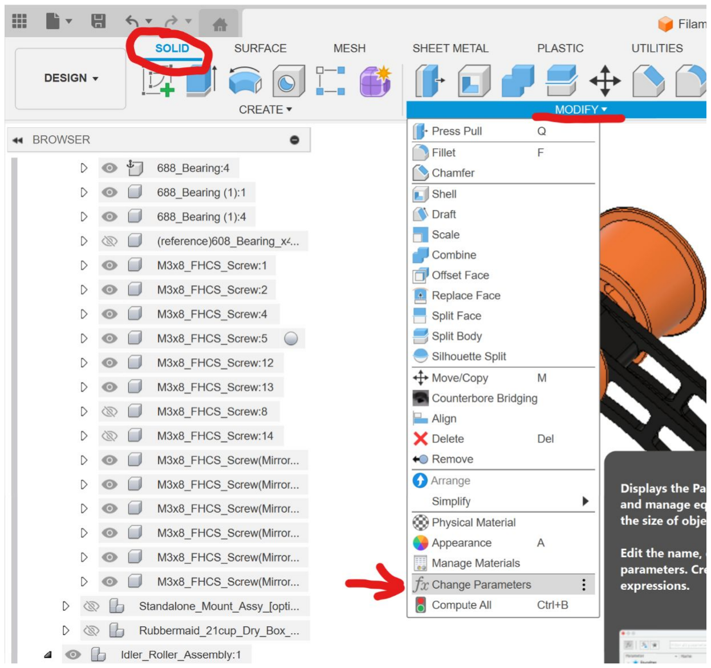
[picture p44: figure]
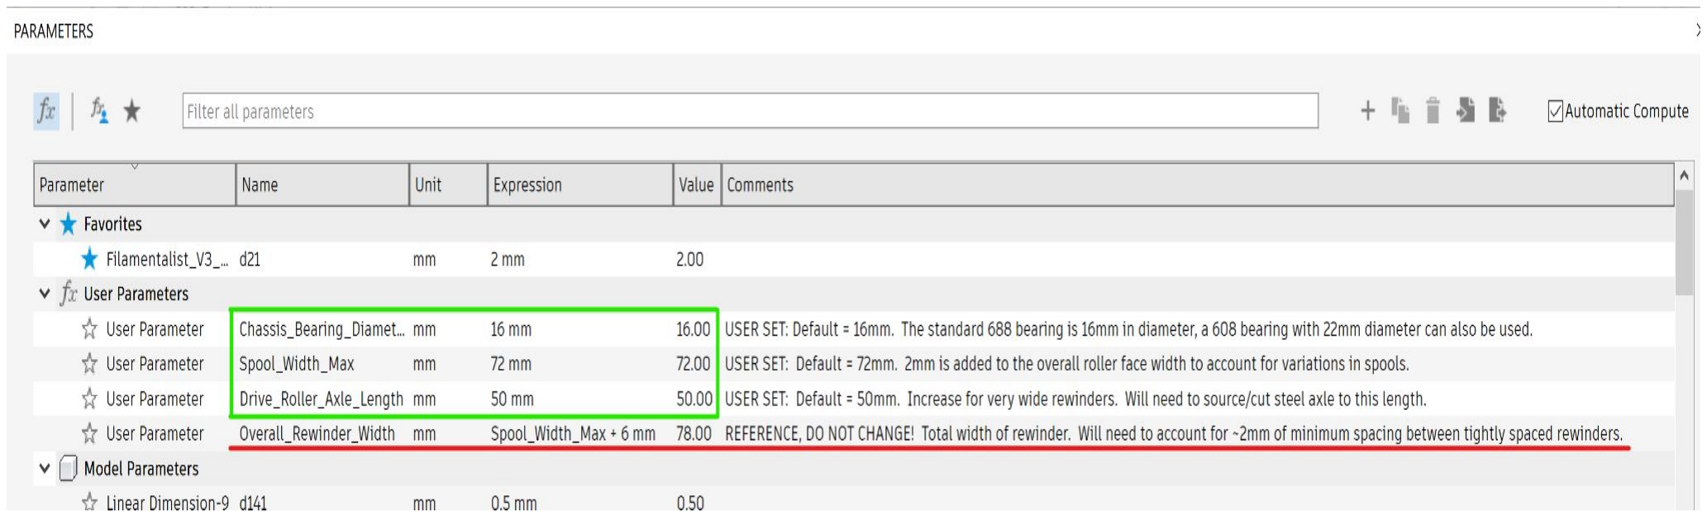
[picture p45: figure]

Adjust the following parameters to meet your needs:
Chassis Bearing Diameter - Set to 16mm if you are using 688 bearings for the Drive and Idler axles or 22mm for 608 bearings. This setting creates unique Chassis_L/R, Rim Roller, and Rear Filamentalist Enclosure Mount parts. Any other setting than 16 or 22mm will result in errors in the model.

(parameter descriptions continued on next page)

ENRAGED RABBIT CARROT FEEDER (ERCF)

INTRODUCTION

THE PARAMETRIC CAD MODEL (continued)

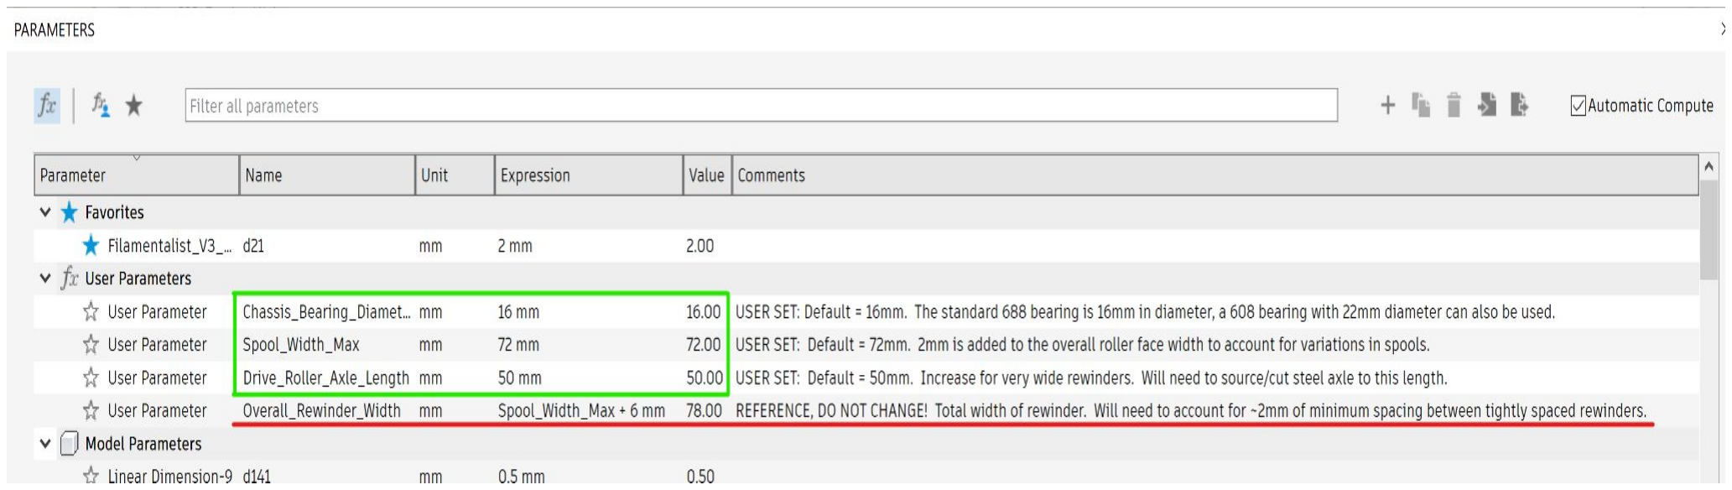
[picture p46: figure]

Adjust the following parameters to meet your needs (continued from previous page):
Spool_Width_Max - The default is 72mm which should accommodate 99% of the 1KG spools on the market. Set this to accommodate the widest filament spool you expect to use. 2mm will be added to this number in the design to allow for spool width and rim straightness/variation.

Drive Roller Axle Length - The default is 50mm. If you already have 80mm axles from the Classic Filamentalist version these can be used with no need to change the parameters in the model. Changing this setting allows you to visualize how a custom (long) axle length will fit, especially if you increase the Spool_Width_Max parameter for a custom wide rewinder.

Overall_Rewinder_Width: REFERENCE PARAMETER. DO NOT CHANGE THIS! This is included as an aid to assess the results of your inputs. You can iterate with changes to the above user inputs to arrive at the desired Overall Rewinder Width for your space, enclosure. Or application.

The model will update to show the results of these parameters to help you visualize the acceptability of the result.

### OVERVIEW

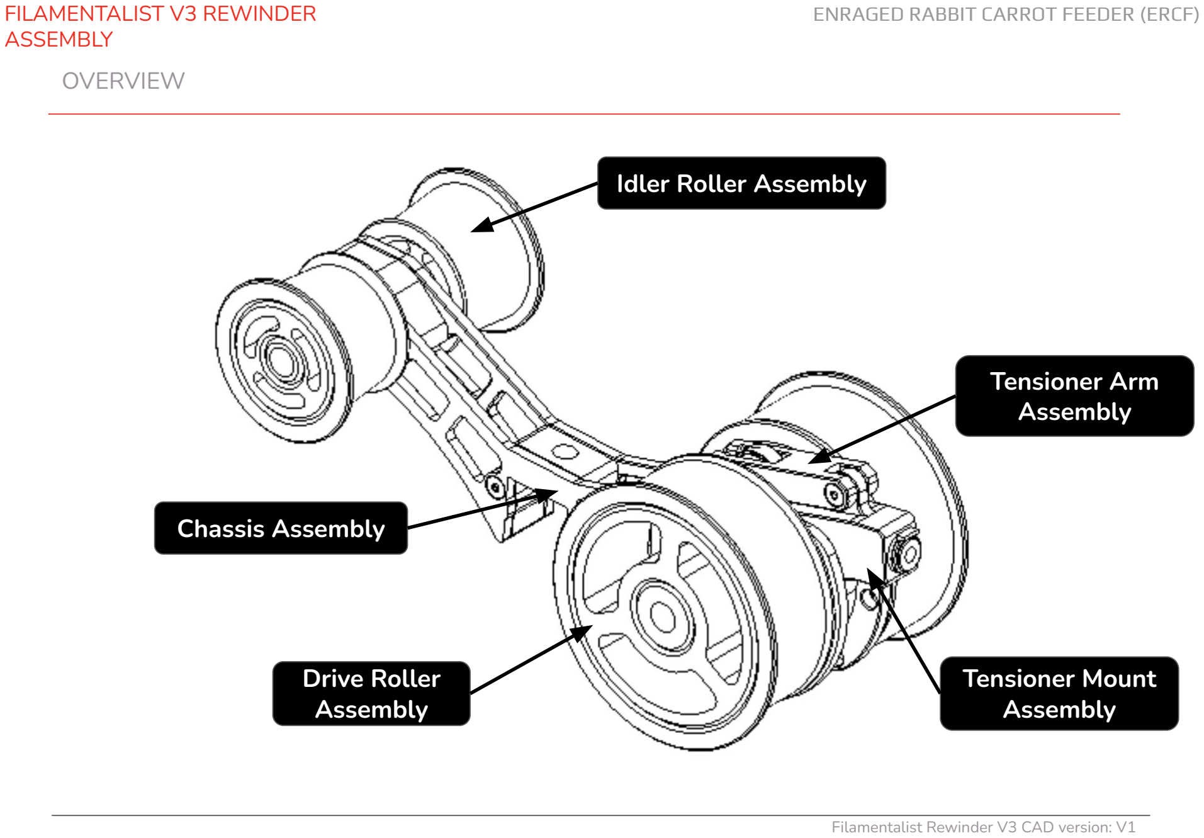
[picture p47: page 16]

ENRAGED RABBIT CARROT FEEDER (ERCF)

FILAMENTALIST V3 REWINDER
ASSEMBLY

## Drive Roller Assembly

## Idler Roller Assembly

## Chassis Assembly

## Tensioner Arm Assembly

## Tensioner Mount Assembly

ENRAGED RABBIT CARROT FEEDER (ERCF)

TENSIONER ARM ASSEMBLY

### EXPLODED VIEW

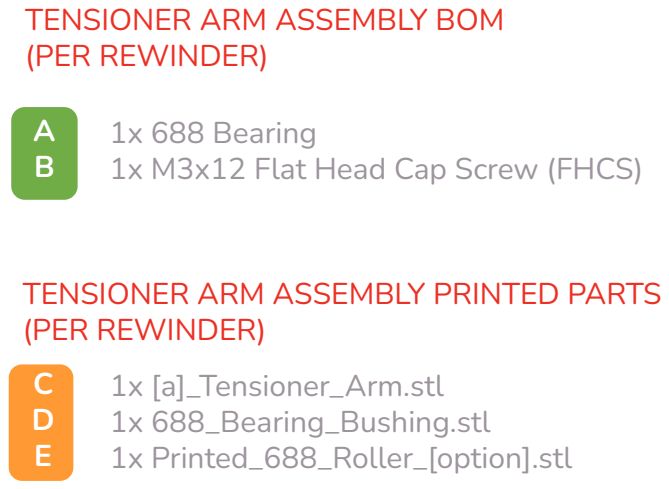
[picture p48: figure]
TENSIONER ARM ASSEMBLY BOM (PER REWINDER); 1x 688 Bearing 1x M3x12 Flat Head Cap Screw (FHCS); 1x [a]_Tensioner_Arm.stl 1x 688_Bearing_Bushing.stl 1x Printed_688_Roller_[option].stl; TENSIONER ARM ASSEMBLY PRINTED PARTS (PER REWINDER)

### ASSEMBLY INSTRUCTIONS

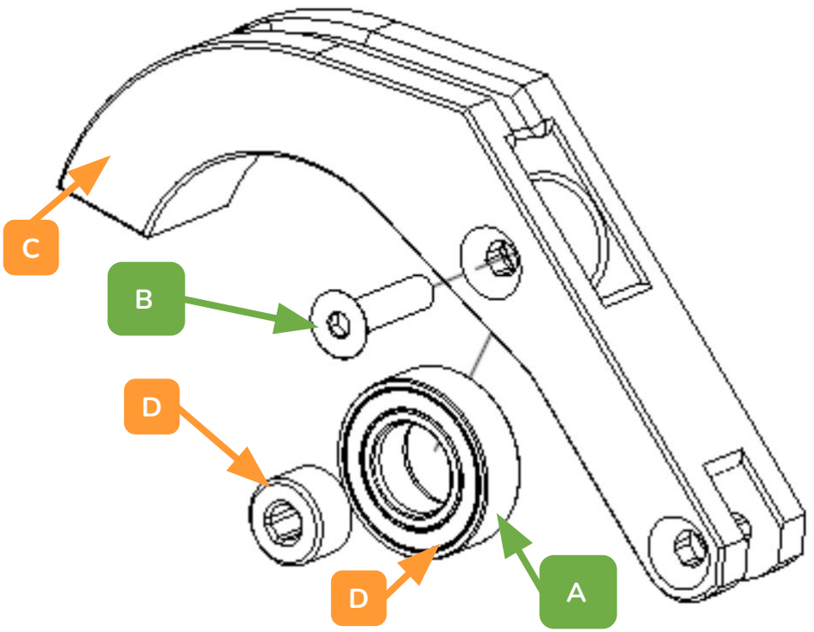
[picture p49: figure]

1. **Note: If you don’t have or want to use a 688 bearing in the Tensioner Arm, the Printed_688_Roller_[option].stl file is provided to use instead.
2. Insert the 688 Bearing Bushing printed part into 688 bearing bore and slide up into Tensioner Arm printed part.
3. Place M3x12 FHCS screw into Tensioner Arm and through the 688 Bearing Bushing and 688 Bearing, cutting threads into plastic of the Tensioner Arm. Only moderate force is required to cut the threads and secure the 688 bearing. Turning the screw with too much force will strip out the plastic threads.

ENRAGED RABBIT CARROT FEEDER (ERCF)

TENSIONER MOUNT
ASSEMBLY
TENSIONER MOUNT ASSEMBLY BOM | EXPLODED VIEW
(PER REWINDER)

1x Heat Set Insert
| 1x ECAS04 1x ECAS04 Locking Clip (stl is available to print)

TENSIONER MOUNT ASSEMBLY PRINTED PARTS

A
B
C

C

D

E

1x ECAS_Clip_[optional_print].stl
(print if not included with ECAS04 purchased part) 1x Tensioner_Mount_Std.stl
or
1xTensioner_Mount_Microswitch_[option].stl
(see next page)
Built-in support that is part of the Tensioner_Mount stl’s but needs to be included if making stl from CAD files)

(PER REWINDER)

D

B

### ASSEMBLY INSTRUCTIONS

1. Remove built-in support (part E) from Tensioner Mount part. A small flat bladed screwdriver placed in the notch works well.
2. Install the heatset insert into the Tensioner Mount part.
3. Insert the ECAS04 into the Tensioner Mount. This should be a tight press fit. One method for installing is to place the ECAS04 on a sturdy surface like a table or counter top and press the Tensioner Mount part downward onto the ECAS04. Ensure the ECAS04 is fully seated against, and aligned to the face of the Tensioner Mount. NOTE: once tubing is installed, secure with an ECAS Locking Clip. If clips were not provided, the ECAS_Clip_[optional_print].stl can be printed.
4. Although not necessary to install now, use of an ECAS04 locking Clip is required once PTFE tubing is installed.
5. If installing a microswitch for filament sensing please refer to the next page.

A

E

C

Tensioner_Mount_Microswitch_[option].stl

Support
removal
notch

C

ENRAGED RABBIT CARROT FEEDER (ERCF)

[OPTIONAL] TENSIONER MOUNT MICROSWITCH ASSEMBLY

### EXPLODED VIEW - LEVER SWITCH

TENSIONER MOUNT MICROSWITCH ASSEMBLY BOM (PER REWINDER)

1x D2F-01FL-D3 Microswitch (lever style)
or
1x D2F-01F-D3 Microswitch (button switch - no lever) 1x MR85 Bearing
or
8x3 Disc Magnet
or
6x3 Disc Magnet
2x M2x8 screws (SHCS or BHCS)

A

B

C

D
E
F

1x Tensioner_Mount_Microswitch_[option].stl
1x 6x3_Magnet_Holder.stl (if using 6x3 magnet)
1x Printed_Switch_Lever.stl (if not using lever switch)

TENSIONER MOUNT MICROSWITCH ASSEMBLY PRINTED PARTS (PER REWINDER)

D

B
MR85 Bearing, or
8x3 Magnet, or
6x3 Magnet in Holder

### ASSEMBLY INSTRUCTIONS

1. Install the MR85 bearing, 8x3 Disc Magnet, or 6x3 Disc Magnet installed in printed 6x3_Magnet_Holder part into the slot in the Tensioner Mount part.
2. If using the button switch (no lever), install the Printed_Switch_Lever printed part into the slot in the Tensioner Mount part. Carefully push back into slots until the barbs click into place.
3. Install the Microswitch into the Tensioner Mount using the M2 screws, cutting threads into the plastic.

A

C

E

### EXPLODED VIEW - BUTTON SWITCH

F

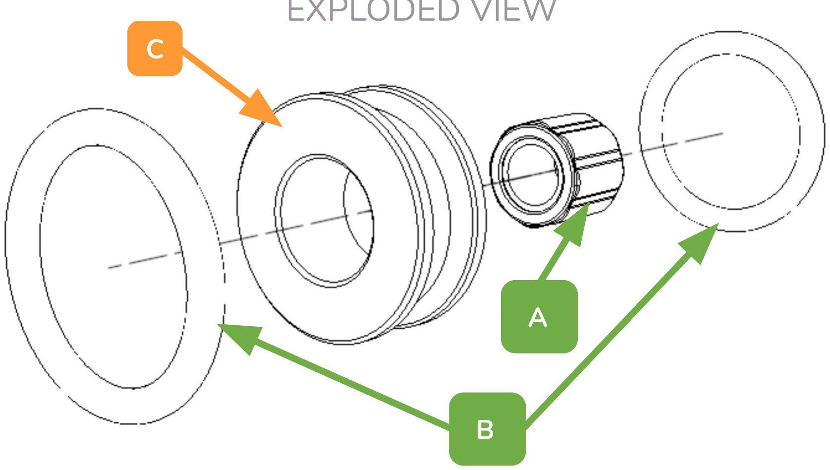
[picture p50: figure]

ENRAGED RABBIT CARROT FEEDER (ERCF)

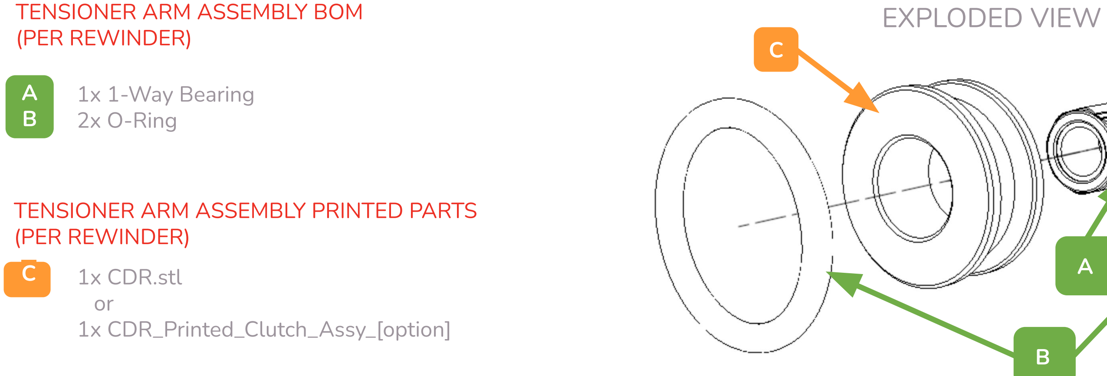
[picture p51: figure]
TENSIONER ARM ASSEMBLY BOM; EXPLODED VIEW; (PER REWINDER); 1x 1-Way Bearing; 2x O-Ring; C 1x CDR.stl or 1x CDR_Printed_Clutch_Assy_[option]; TENSIONER ARM ASSEMBLY PRINTED PARTS (PER REWINDER)

CENTER DRIVE ROLLER (CDR)
ASSEMBLY

### ASSEMBLY INSTRUCTIONS

1. Press the 1-Way Bearing into the CDR part. A bench vise, c-clamp, quick-grip/trigger ratcheting clamp, or soft jaw pliers can be used. Ensure the 1-Way bearing is centered within the CDR.
2. Stretch the (2) o-rings onto the CDR.

### EXPLODED VIEW

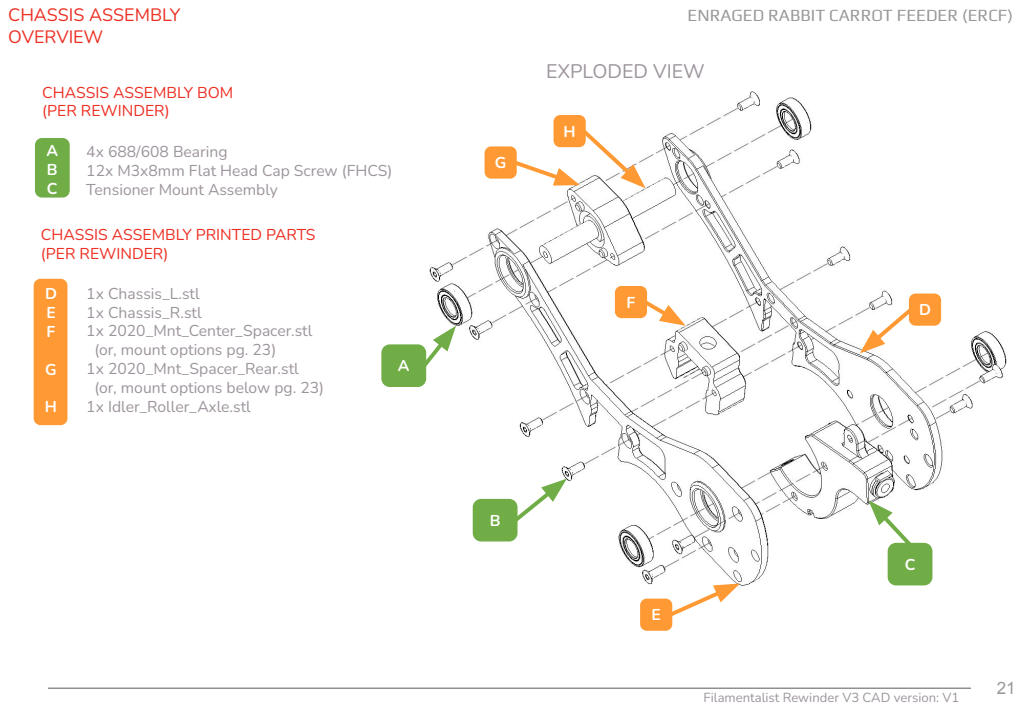
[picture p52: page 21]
CHASSIS ASSEMBLY OVERVIEW; 1x Chassis_L.stl 1x Chassis_R.stl 1x 2020_Mnt_Center_Spacer.stl (or, mount options pg. 23) 1x 2020_Mnt_Spacer_Rear.stl (or, mount options below pg. 23) 1x Idler_Roller_Axle.stl

ENRAGED RABBIT CARROT FEEDER (ERCF)

CHASSIS ASSEMBLY BOM
(PER REWINDER)

4x 688/608 Bearing
12x M3x8mm Flat Head Cap Screw (FHCS)
Tensioner Mount Assembly

CHASSIS ASSEMBLY PRINTED PARTS

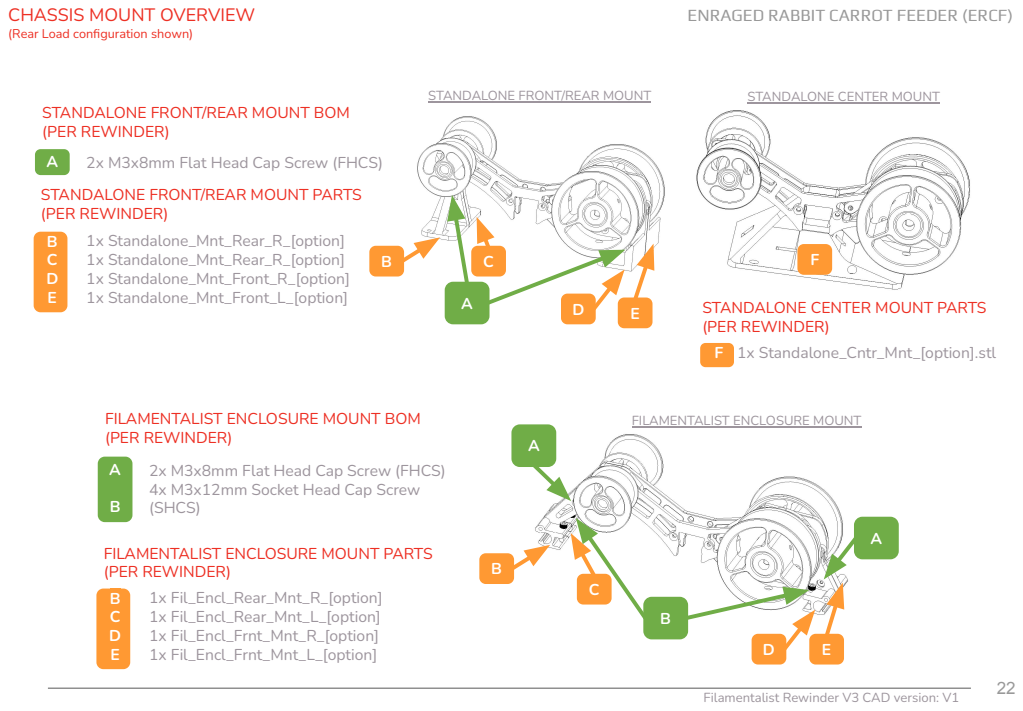
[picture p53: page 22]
FILAMENTALIST ENCLOSURE MOUNT PARTS (PER REWINDER); 1x Fil_Encl_Rear_Mnt_R_[option] 1x Fil_Encl_Rear_Mnt_L_[option] 1x Fil_Encl_Frnt_Mnt_R_[option] 1x Fil_Encl_Frnt_Mnt_L_[option]

CHASSIS MOUNT OVERVIEW
(Rear Load configuration shown)

ENRAGED RABBIT CARROT FEEDER (ERCF)

STANDALONE FRONT/REAR MOUNT

STANDALONE CENTER MOUNT

STANDALONE FRONT/REAR MOUNT BOM
(PER REWINDER)
A 2x M3x8mm Flat Head Cap Screw (FHCS)
STANDALONE FRONT/REAR MOUNT PARTS
1x Standalone_Mnt_Rear_R_[option]
1x Standalone_Mnt_Front_R_[option]
1x Standalone_Mnt_Front_L_[option]

STANDALONE CENTER MOUNT PARTS
F 1x Standalone_Cntr_Mnt_[option].stl

FILAMENTALIST ENCLOSURE MOUNT BOM
2x M3x8mm Flat Head Cap Screw (FHCS)
4x M3x12mm Socket Head Cap Screw
(SHCS)

FILAMENTALIST ENCLOSURE MOUNT

ENRAGED RABBIT CARROT FEEDER (ERCF)

CHASSIS ASSEMBLY - STEP 1

### ASSEMBLY INSTRUCTIONS

1. Hand press (2) 688 or 608 bearings (depending on version printed) into
the bearing pockets of the Chassis_R part.
2. Align the pegs of 2020_Mnt_Rear_Spacer with the peg pockets in Chassis_R and secure with (2) M3x8mm FHCS screws.
2.1. If using Filamentalist Enclosure mounts use Fil_Encl_Rear_Mnt_R_[option] in place of the Spacer part (see next page).
3. Align the pegs of 2020_Mnt_Center_Spacer with peg pockets in Chassis_R part and secure with (2) M3x8mm FHCS screws.
3.1. If not mounting to a 2020 center rail and you want a stiffer chassis, install the 1x Chassis_Cntr_Spacer_[option]. If using the center Standalone mount then install the 1x Standalone_Mnt_R_[option]
3.2. Or, if using the Standalone mount install the Standalone_Cntr_Mnt part.
4. Secure the Tensioner Mount assembly with (2) M3x8mm FHCS screws in either the front or rear load orientation.
CHASSIS ASSEMBLY BOM | EXPLODED VIEW
(PER REWINDER)
2x 688/608 Bearing
6x M3x8mm Flat Head Cap Screw (FHCS)
Tensioner Mount Assembly

E
F

G

1x Chassis_R.stl
1x 2020_Mnt_Center_Spacer.stl
(or, see Chassis Mount options pg. 22) 1x 2020_Mnt_Rear_Spacer.stl
(or, see Chassis Mount options pg. 22)

CHASSIS ASSEMBLY PRINTED PARTS (PER REWINDER)

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
(FRONT LOAD
ORIENTATION)

C
(REAR LOAD
ORIENTATION)

ENRAGED RABBIT CARROT FEEDER (ERCF)

CHASSIS ASSEMBLY - STEP 2

### ASSEMBLY INSTRUCTIONS

1. Hand press (2) 688 or 608 bearings (depending on version printed) into
the bearing pockets of the Chassis_L part.
2. Insert the Idler_Roller_Axle part through the 2020_Mount_Rear_Spacer part and bearing.
3. If using the Filamentalist Enclosure or Front/Rear Standalone Mount options (see pg. 22), screw the two front mounts together with a M3x8 FHCS screw and insert into the peg holes at the front of the Chassis_R part.
4. Secure the Chassis_L part with (6) M3x8mm FHCS screws at the 2020_Mnt_Center_Spacer, 2020_Mnt_Rear_Spacer, and Tensioner Mount Assembly aligning hole locations.

### EXPLODED VIEW

CHASSIS ASSEMBLY BOM
(PER REWINDER)

2x 688/608 Bearing
6x M3x8mm Flat Head Cap Screw (FHCS)

C
D

1x Chassis_L.stl
1x Idler_Roller_Axle.stl

CHASSIS ASSEMBLY PRINTED PARTS (PER REWINDER)

A
B

A

B
C D

ENRAGED RABBIT CARROT FEEDER (ERCF)

CDR/TENSIONER ARM ASSEMBLY

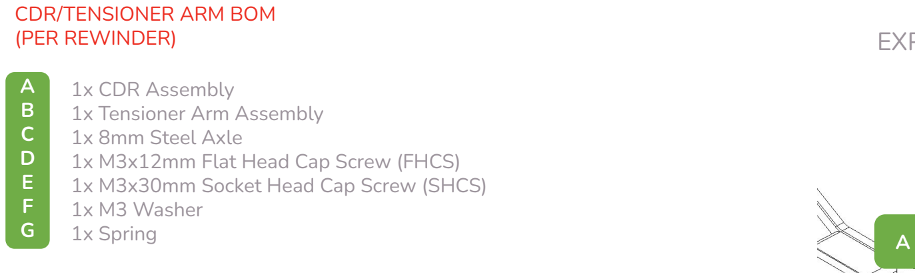
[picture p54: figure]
CDR/TENSIONER ARM BOM (PER REWINDER); 1x CDR Assembly 1x Tensioner Arm Assembly 1x 8mm Steel Axle 1x M3x12mm Flat Head Cap Screw (FHCS) 1x M3x30mm Socket Head Cap Screw (SHCS) 1x M3 Washer 1x Spring

### ASSEMBLY INSTRUCTIONS

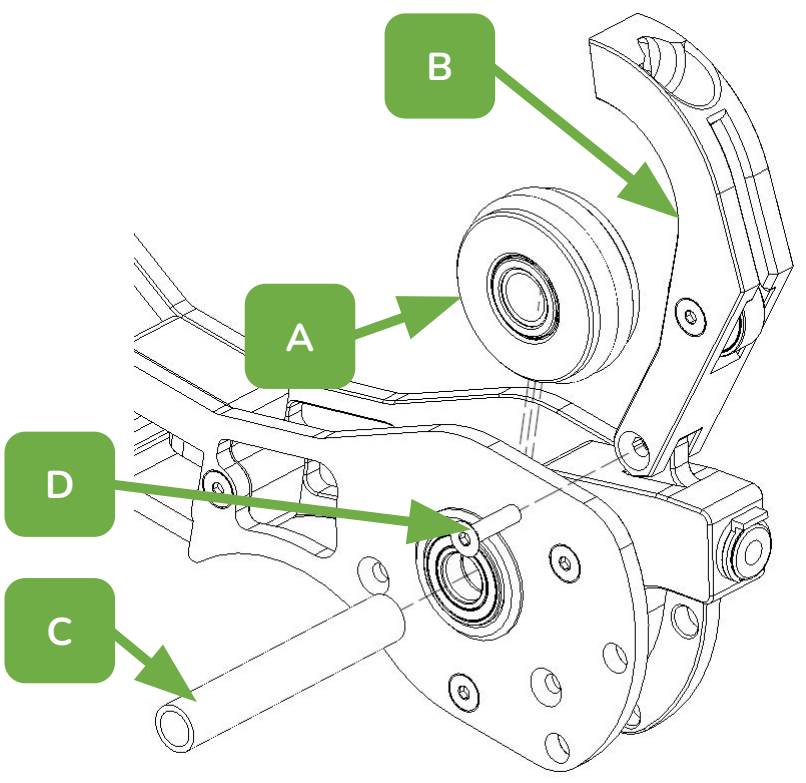
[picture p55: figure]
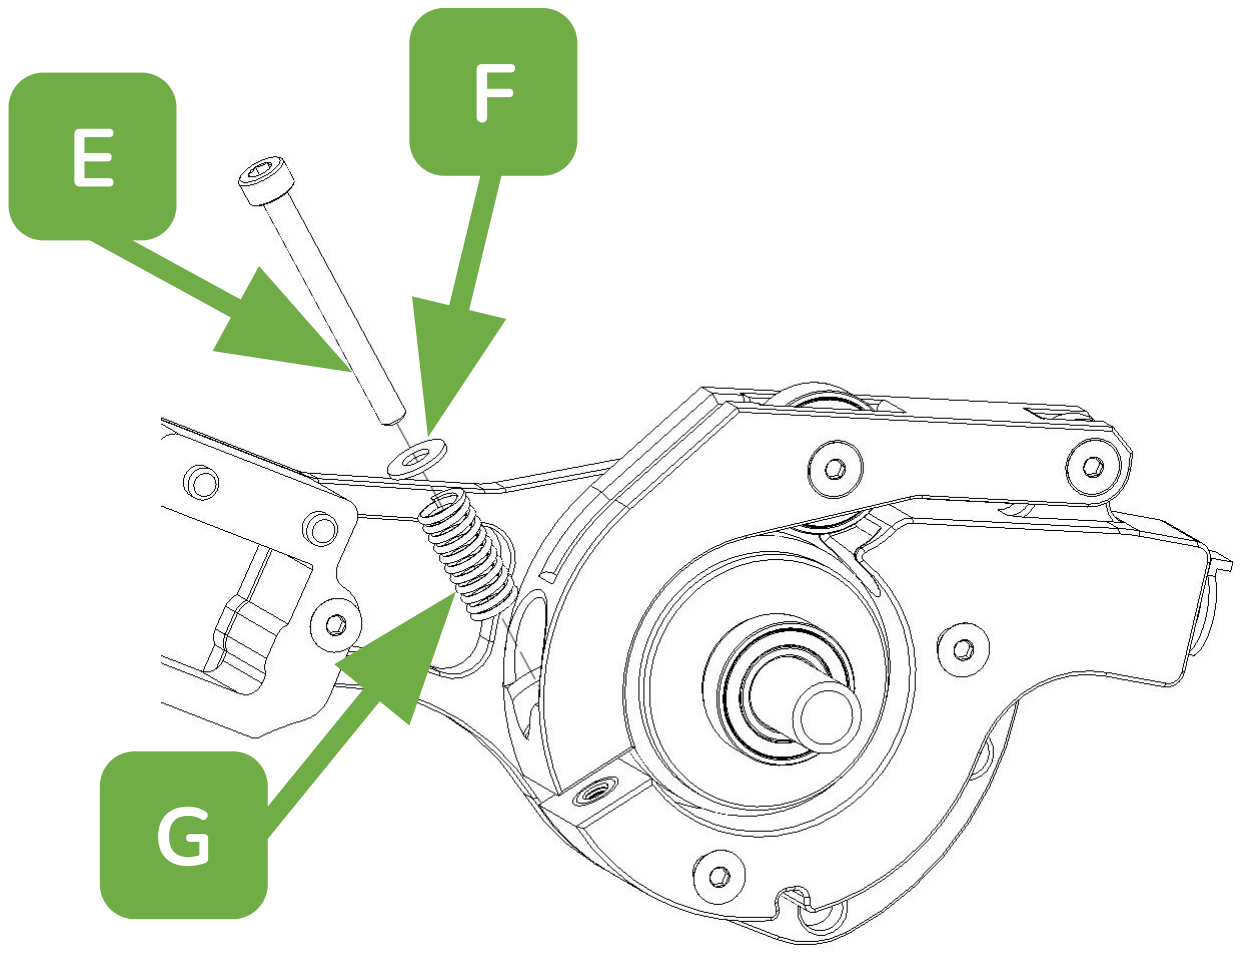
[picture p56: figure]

1. Attach Tensioner Arm Assembly with 1x M3X12mm Flat Head Cap Screw (FHCS)
2. Check for correct CDR/One-Way bearing orientation per pg. 27 and then drop CDR Assembly into Tensioner Mount “pocket”.
3. Insert 8mm axle through chassis bearings and CDR assembly.
4. Verify correct CDR/One-Way bearing orientation per pg. 27 and repeat steps 2 and 3 if necessary.
5. Place an M3 washer followed by the spring onto a M3x30 SHCS screw, insert through slot in Tensioner Arm, and screw into heat set insert in the Tensioner Mount (leave spring untensioned for now).

### EXPLODED VIEWS

ENRAGED RABBIT CARROT FEEDER (ERCF)

ONE-WAY BEARING ORIENTATION

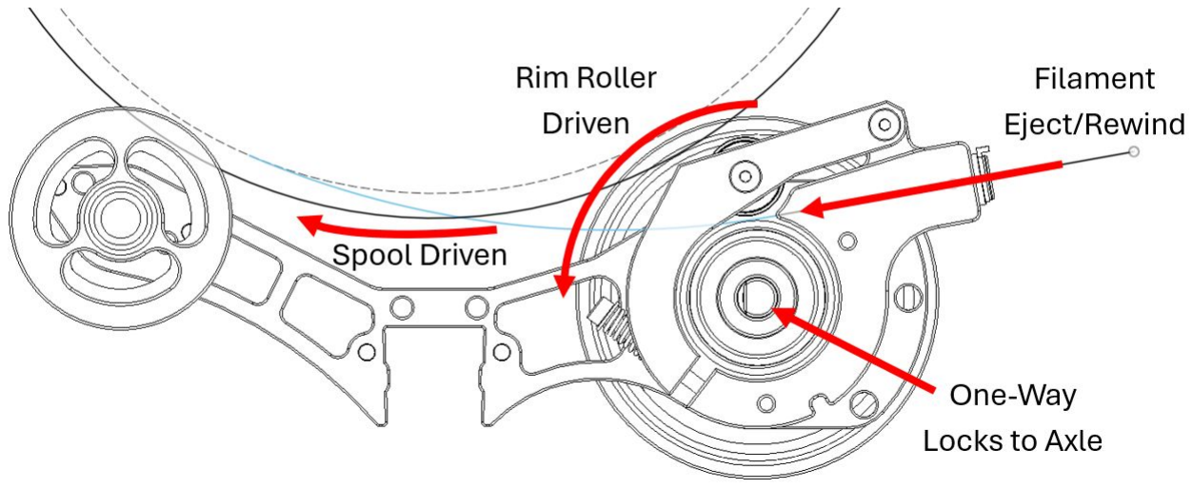
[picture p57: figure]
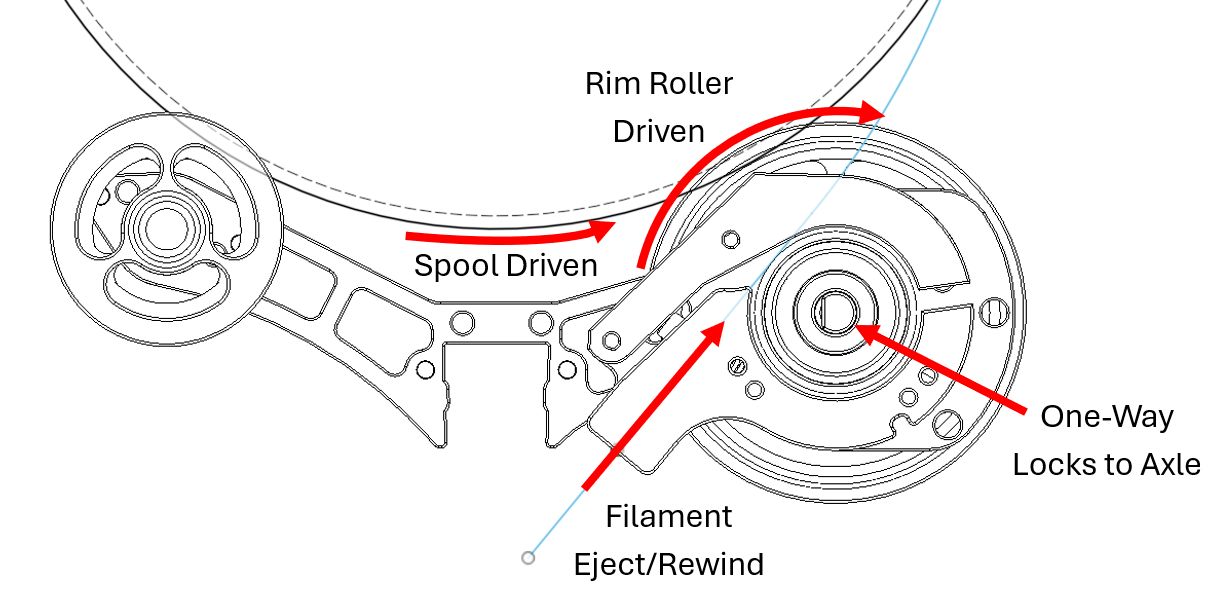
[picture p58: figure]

One-Way bearing locks when Rim Roller/Axle is held and Center Drive Roller is rotated in the direction of filament unload/eject (in the pictures above clockwise for front load configuration, counter clockwise for rear/bottom load)

FRONT LOAD CONFIGURATION | REAR/BOTTOM LOAD CONFIGURATION

ENRAGED RABBIT CARROT FEEDER (ERCF)

### RIM/IDLER ROLLER ASSEMBLY

### ASSEMBLY INSTRUCTIONS

1. Stretch Rubber Bands onto Rim Rollers.
2. Ensure axle is centered within the chassis bearings within +/-1mm.
3. Slide Rim Rollers onto steel axle and flush against chassis bearings. Insert M3 screws (length 12mm through 16mm) and tighten with moderate pressure against axle. Ensure Rim Rollers do not compress chassis inward checking that the Tensioner arm can move freely between the chassis parts.
4. Slide Idler Rollers onto Idler Axle. Drive M3x12mm FHCS screws will be driven through the thin support web on the Idler Roller and into the Idler Axle.
RIM/IDLER ROLLER BOM | EXPLODED VIEW
(PER REWINDER)

2x Rubber Band
2x M3x12-16mm Screw (Socket Head preferred)
2x M3x12mm Flat Head Cap Screw (FHCS)

D
E

2x Rim Roller
2x Idler Roller

RIM/IDLER ROLLER PRINTED PARTS (PER REWINDER)

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
ENRAGED RABBIT CARROT FEEDER (ERCF)

### TUNING INSTRUCTIONS

Tune by setting the Tensioner Arm clamping force. The Tensioner Arm does not need an extreme amount of tension.
1. As a bench test (not connected to the MMU yet), insert an ~500mm length of filament into the Tensioner Arm slot, through the o-ring/bearing interface, and out the ECAS side of the Tensioner Mount.
2. Hold one RimRoller and try to pull the filament out in the eject direction.
3. The slip force/resistance should “light-to-moderate” (~0.2-0.3 kg or ~7-10 oz). Adjust the spring tensioner screw accordingly and err on the light side for a starting point.
4. Once a spool is loaded on the rewinder pull ~1m of filament in the load direction. Filament should stay tight on the spool (no loose loops). If loose loops form this indicates that the One-Way Bearing/Center Drive Assembly may be installed backwards (return to CDR/TENSIONER ARM ASSEMBLY step), or the One-Way bearing is too tight on the Center Drive Roller Axle (see Filamentalist Troubleshooting Guide (https://github.com/Enraged-Rabbit-Community/ERCF_v2/blob/master/Recommended_Options/Filamentalist_Rewinder/troubleshoot.md) .).
5. Starting with a tightly packed filament roll, push filament back onto the spool to simulate an MMU unload/eject. If loose filament is forming around the filament spool during unload, tighten the spring tensioning screw. If no loose filament is forming around the filament roll, gradually reduce the spring tension until loose filament starts to accumulate and then increase tension in ~1/2 screw turn increments until you feel you have the lightest tension that results in a tightly packed unload.
6. Initial tuning is complete and the rewinder can now be installed into your system. Steps 4 and 5 above can be followed after rewinder installation if additional tuning is required.

Filament
unload/eject
direction

Filament
load/extrude
direction

Feed filament
through slot in
Tensioner Arm

ENRAGED RABBIT CARROT FEEDER (ERCF)

### O-RING REPLACEMENT

You may never need to replace o-rings. Testing and extrapolation estimates that the wear-out point is greater than 5000 cycles. The impact of o-ring wear-out can be reduced by periodically swapping highly used rewinders with low use rewinders in your line-up. Also, o-rings with grooves worn in them can be swapped with their opposing partners to present the unworn side/face to the filament to extend the life of a set. For o-ring replacement, FOLLOW THE STEPS BELOW:

1. Remove one Rim Roller and slide drive axle out of the rewinder.
2. Unscrew the M3x30mm Tensioner Screw, pivot the Tensioner Arm out of the way, and remove the CDR Assembly.
3. Remove the old o-rings (a dental pic or small flat bladed screwdriver works great).
4. Install a new pair of o-rings or reposition the worn o-rings to present unworn surfaces to the filament interface.
5. Replace the “fresh” CDR Assembly back into the rewinder verifying that the Center Drive Roller Assembly/One-Way Bearing is in the correct orientation (see pg. 27) and reassemble the unit.

ENRAGED RABBIT CARROT FEEDER (ERCF)

Questions, Troubleshooting,
and Help
1. If your rewinder is not functioning properly please reference the Troubleshooting guide on Github here: https://github.com/Enraged-Rabbit-Community/ERCF_v2/blob/master/Recommended_Options/Filamentalist_Rewinder/troubleshoot.md (https://github.com/Enraged-Rabbit-Community/ERCF_v2/blob/master/Recommended_Options/Filamentalist_Rewinder/troubleshoot.md)
a. A video demonstrating the heat rework procedure for tight one-way bearings can be found at 4:20 in the Assembly Video here: https://youtu.be/-1cHOcnosxE
2. Common questions are answered in the FAQ on Github here: https://github.com/Enraged-Rabbit-Community/ERCF_v2/blob/master/Recommended_Options/Filamentalist_Rewinder/Filamentalist_FAQ.md (https://github.com/Enraged-Rabbit-Community/ERCF_v2/blob/master/Recommended_Options/Filamentalist_Rewinder/Filamentalist_FAQ.md)
3. There is an active community supporting and improving the Filamentalist rewinder on Discord here:
https://discord.gg/hxe9eMWseT

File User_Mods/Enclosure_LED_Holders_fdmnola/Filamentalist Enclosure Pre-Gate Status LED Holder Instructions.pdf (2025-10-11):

Filamentalist Enclosure Pre-Gate Status LED Holder


I wanted to have pre-gate status indicator LEDs for my ERCF V2 using the Filamentalist Enclosure. There weren’t any designs available that I liked so I designed these simple and quick holders that snap into the front 2020 extrusions in front of each Filamentalist inside the enclosure. I also designed a double stack holder with arrows that points to the side of the enclosure for spools mounted outside of the enclosure (for 8+ lane builds).
Shoutouts:
- SkiBikeMake- for his awesome rewinder and enclosure designs
- PrintSomething- for his lens design that I used to make this
- Moggieuk- For the Happy Hare software that controls the LEDs

BOM:
- Filament – I used ABS, however other filaments should work fine since the enclosure isn’t heated. You’ll need the color you want the holder to be, plus a clear or opaque for the lenses
- Round WS2812 5050 button LEDs – I used the pre-gate LEDs included in my Siboor ERCF V2 kit, but these have also been tested to fit: https://a.aliexpress.com/_mLgbtSN
- Wire – Smaller gage wires work best, I used 28 gage wire I had on hand

Printed parts:
- LED holders – one per channel in the enclosure, double for external rolls
- LED lenses – one per channel in enclosure, double with arrow for external rolls. Number, size, and font can be changed in the f3d file here:

- 2020 Extrusion Cover (Optional) – Used to hold wires inside of the extrusion between led holders. Length determined by the width and spacing of your Filamentalists. I use these: https://www.thingiverse.com/thing:4881812

Print settings:
- LED holders are best printed on their side
- LED lenses are printed flat on the bed, and solid infill or max walls. Multi color, or include a filament swap in your slicer of choice. (I swap filament at layer 16)
- Standard Voron settings with supports turned on for the LED holders. I prefer auto tree supports in Orca Slicer which works out very well

Tools:
- Soldering iron and solder – to connect wires to the LEDs
- Side cutters, or razor blade – to remove the built in supports

Build:


Note:
These instructions assume you are familiar with LED wiring and route your 5VDC and LED signal wires to the first LED. You can be as creative with this as you want, I routed mine through the center of the enclosure between channels 2 and 3, then through the extrusion behind LED holders 0,1, and 2 to connect to the input of the channel 0 LED
- Determine wire length needed and cut to wires appropriately. 120mm minimum recommended length between standard 78mm width V3 filamentalist units, a little extra is fine, but too much will be difficult to stash in the extrusions
- Solder the wires to the LEDs. Be careful not to use an excess of solder as it may interfere with the fit inside the LED holder assembly. Pay attention to the direction of signal injection when soldering, the arrows need to point in the same direction
- Remove built in supports from the led holders. These can be cut off with a razor knife or side cutters


Note:
The top two built in supports do not need to be removed if you feed wires through before soldering to the individual LEDs, but it is much simpler to remove the supports and solder the LEDs before installing
- Insert each individual LED into a holder by lifting the lever tab and sliding the led into place. Ensure the LED is centered in the hole and the PCB is flush against the LED holder body. The lever tab will hold the LED in place. Repeat for each LED holder. Double LED holders are assembled in the same fashion, but two LEDs are installed – these can be a little fiddly to get the LEDs into place, but it is doable with a little patience


- Install LED windows into the LED holders, they are designed to be a friction fit and should snap into place nicely as long as your printer is tuned to Voron and Filamentalist specifications

Support removal locations


- Install the first LED holder into 2020 extrusion in the desired position. They are designed to be a snap fit and can be slid along the extrusion once installed if necessary. Route wires through the channel in the LED holder and into the extrusion under the side ‘fingers’ that will hold the wires in the channel and guide them into the extrusion. Repeat for each LED holder

Extrusion Cover; Wiring routed behind ‘finger’

- Optionally, install extrusion fillers into the 2020 extrusion between the LED holders to hold the wiring inside of the extrusion
- Configure your LEDs in Happy Hare as desired and enjoy!

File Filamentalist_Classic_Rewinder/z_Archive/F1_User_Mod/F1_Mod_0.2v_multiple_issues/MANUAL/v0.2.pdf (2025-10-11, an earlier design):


M3 nut

M3 bolt 6mm


M3 insert nut

M3 insert nut


623 Bearing

M3 bolt 18mm


6x3 magnets


6x3 magnets


M3 bolt 18mm


608 bearing


clutch bearing

O ring x 2


8mm shaft

M3 bolt 8mm

M3 bolt 8mm

M3 bolt 8mm

M3 bolt 8mm


M3 bolt 8mm

M3 bolt 8mm

M3 bolt 8mm


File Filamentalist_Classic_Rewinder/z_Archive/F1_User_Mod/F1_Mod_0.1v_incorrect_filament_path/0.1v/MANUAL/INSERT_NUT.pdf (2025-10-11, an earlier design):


M3 INSERT NUT X 3


M3 INSERT NUT X 3

623 BEARING X 2


M3 INSERT NUT X 4

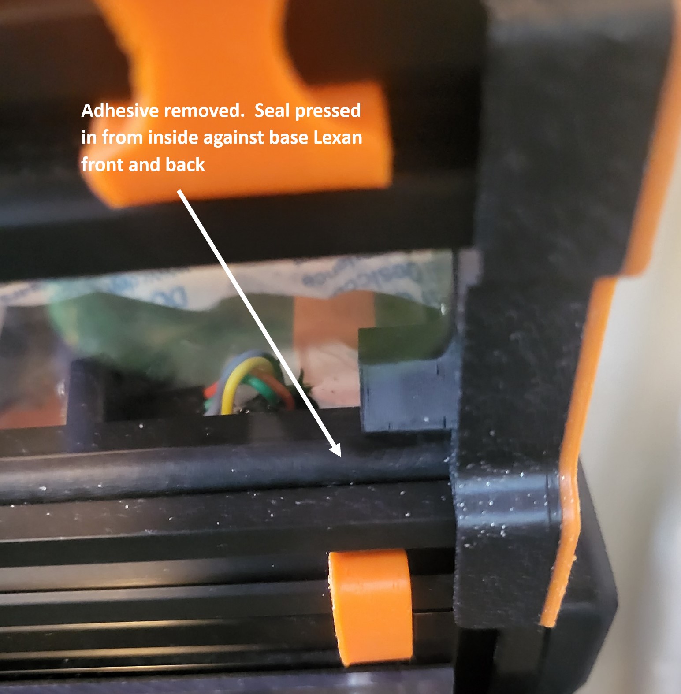
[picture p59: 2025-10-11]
Assets/Enclosure/Seal_Install_5.jpg

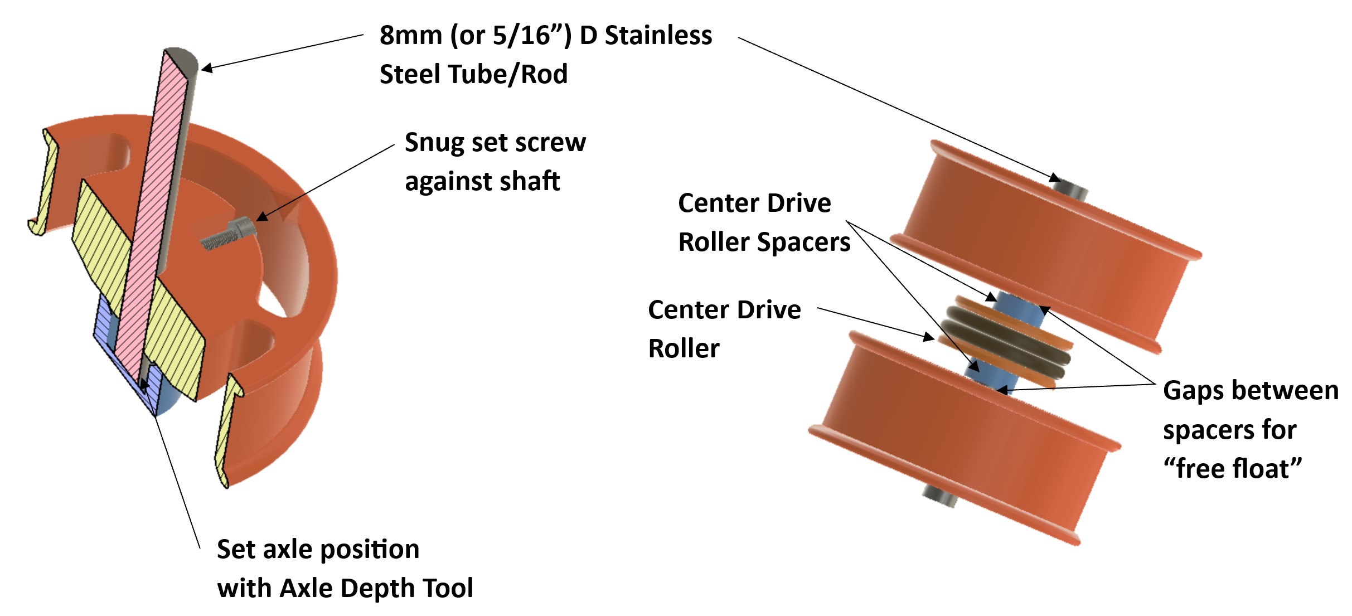
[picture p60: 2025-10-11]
Assets/Drive_Roller_Assembly_1.jpg

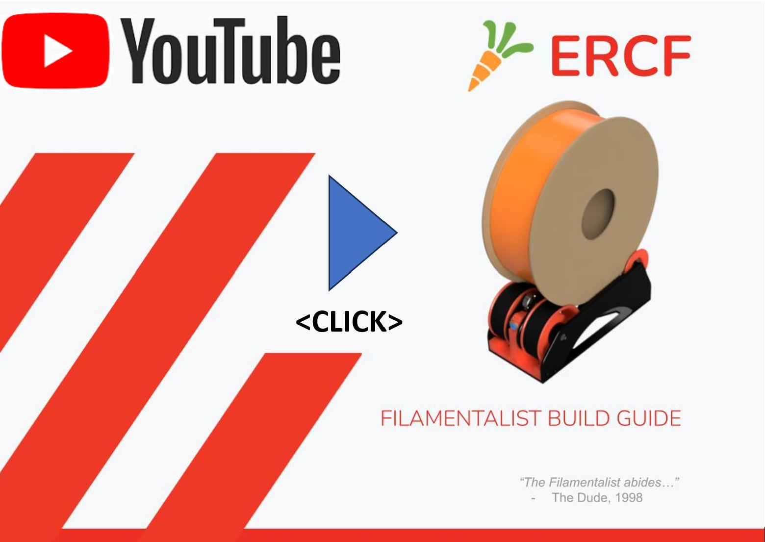
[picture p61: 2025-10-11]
Assets/Filamentalist Assembly Video Thumbnail.jpg

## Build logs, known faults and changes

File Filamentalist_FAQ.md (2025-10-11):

# Filamentalist Frequently Asked Questions

[1. Troubleshooting](#troubleshooting)

[2. Dimensions/Footprint](#dimensions-footprint)

[3. Enclosure Solutions](#enclosure-solutions)

[4. Gear motor recommendations and 40 tooth mod](#gear-motor-options)

[5. Pregate Sensor Solutions](#pregate-sensor-solutions)

[6. Rubber Band Sourcing Options](#rubber-band-sourcing-options)

[7. TPU - Can the Filamentalist handle soft/flexible materials?](#flexible-filament)

## Troubleshooting
- If you have built the Filamentalist(s) and are having issues with its functioning such as loose loops or gear motor stalling please refer to this [Trouble Shooting Guide](https://github.com/SkiBikePrint/Filamentalist/blob/9d7a90dc3dec40c67051558c80c616155eb8eba8/troubleshoot.md).  If this doesn't help to resolve your questions you can get help from the many great users at the Filamentalist Discord server here (https://discord.gg/uDcGxukRKd)

## Dimensions Footprint
- Length:  186mm
  - Length with 200mm Diameter Spool:  202mm
- Height:  76mm without optional Base Plate, 79mm with Base Plate
  - Height with 200mm Diameter Spool:  252mm without optional Base Plate, 255 with Base Plate (varies slightly with Rim Roller rubber band thickness)
- Width:  80mm Axle Version = 81.5mm **(max spool width of 68mm)**, 100 mm Axle Version = 100mm **(max spool width of 86.5mm)** <br />
  <br />
    
[return to index](#filamentalist-frequently-asked-questions)

## Enclosure Solutions

  ### Filamentalist Enclosure

  An elegant passive enclosure/dry box (no heaters or fans) designed to house the Filamentalist passive rewinder.  It is great for a 4-6 channel ERCF (can go to higher channels if desired).  It consists of (4) printed endcaps, (6) pieces of 2020 extrusion cut/ordered to the desired length, and 0.060" (1/16') polycarbonate sheet(s) cut to size.  Details and files here:  https://github.com/SkiBikePrint/ERCF_Mods/tree/main/Filamentalist_Enclosure

  

  ### (Un)original Prusa Drybox

  Box is available here:  https://www.printables.com/model/551828-unoriginal-prusa-drybox .  Delete the rollers and add your own Filamentalist mounting solution.  You may need the rear load option for the Filamentalist

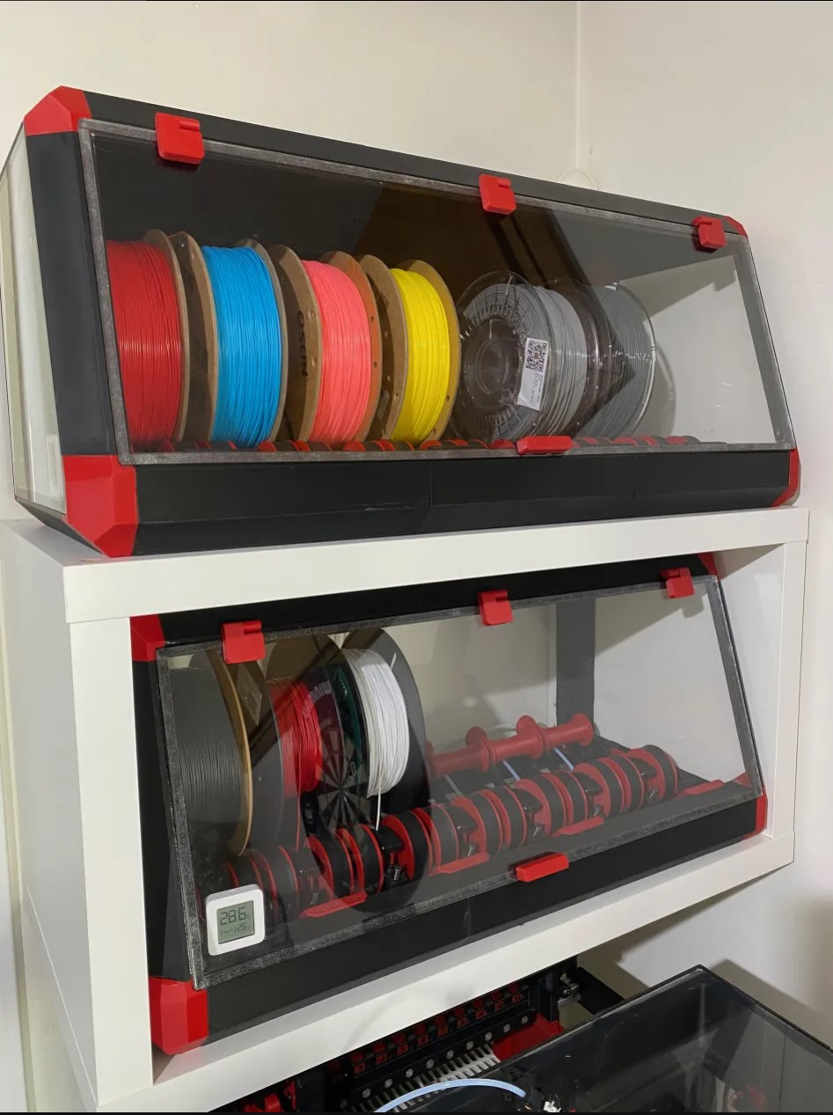
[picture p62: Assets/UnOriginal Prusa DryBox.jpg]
  
  (solution/picture courtesy of barsam on Discord)<br />
  <br />
    
  [return to index](#filamentalist-frequently-asked-questions)

## Gear Motor Options

  It is frequently asked if a NEMA 14 gear motor is strong enough to drive an MMU plus Filamentalist.  The 0.8A Moons NEMA 14 motor that came with my ERCF V1 Blurolls kit worked fine with the ERCF V1 and Filamentalist.  When I upgraded to ERCF V2 the additional resistance that came with the "Springy" version of the selector made the system slightly underpowered with a NEMA 14.  So if a NEMA 14 is what you currently have for your ERCF, TradRack, or other MMU, I suggest you try it before buying a higher torque motor.  If you are building a new MMU, then a NEMA 17 with torque greater than 40N-cm is recommended.  

  For the ERCF, Grafton's 40 tooth gear mod is also recommended ( https://www.printables.com/model/692720-ercf-40-tooth-gear-modifiction ). It allows you to use the same belt as is used with the baseline 80 tooth gear by providing a higher motor mount to take up the slack. Some ERCF kits come with a 42Ncm NEMA 17.  This combined with the 40T mod should give you sufficient torque to overcome MMU and long bowden tube resistance as well as allowing to run the Filamentalist at 300+mm/s speeds.  

  If you are buying a new NEMA 17, below are verified high torque motors (55-59Ncm) that perform well in the needed RPM range for 200-500mm/s load/unload speeds.  There is really no need to go higher than the 55-59Ncm torque range as you will just start grinding grooves in your filament with the MMU gear.  There is likely several other stepper motor options that have similar specifications.

1. 17HE19-2004S from stepperonline.com - 55Ncm (they have a new 17HS19-2004S1 50Ncm version that should be similar to the 17HE19-2004S but a little more powerful)
2. LDO-42STH48-2504AC - 55Ncm<br />
  <br />
    
  [return to index](#filamentalist-frequently-asked-questions)

## Pregate Sensor Solutions

  Research the options below and decide what will work best for you.
  
  ### CottonTail Lite:  
  - https://github.com/Tyler8299/CottonTail-Lite
  - Includes:
    - Coupler Blocks
    - End Cap Mount 
    - End Arm Cap Mount
    - End Arm Cap Mount Extension
    - Universal Electronics Box, Lid, and Mount
    - LED Carrier/Apron
  
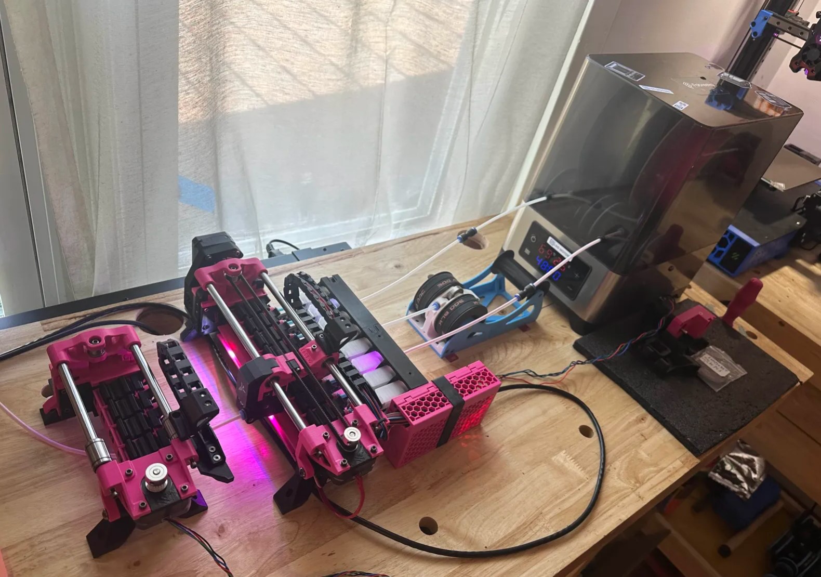
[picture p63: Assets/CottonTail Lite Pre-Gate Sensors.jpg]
  

  ### CheeseFrog's
  https://github.com/juliusjj25/ERCF-Pregate-Sensors

  This is what SkiBikePrint uses (SkiBikeMake (Filamentalist) on Discord).  It is simple and works great.  It requires the "bumped" simulated roller lever style Omron D2F-L3 microswitches.  These are great for a new build.  Retrofitting this onto an existing ERCF requires a tear down of the unit to replace the filament path portion of the blocks as well as the latches.  I did it the brute force way and trimmed my existing latches back with clippers and "muscled" the filament path parts out and back in to the blocks.  The brute force approach may not be for everyone!
  
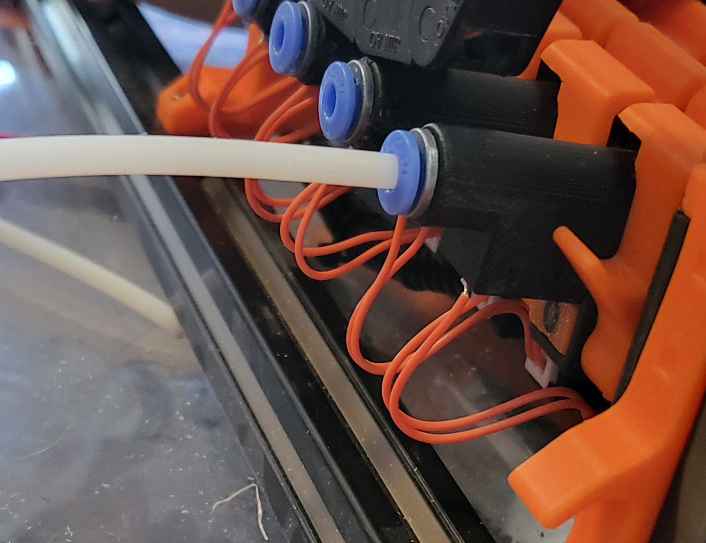
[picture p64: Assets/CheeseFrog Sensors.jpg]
  

  ### Gneu42's Filament Block 
  https://github.com/gneu42/Triple-Decky/tree/main/STL/ERCF-V2/Rev_C/Rev_C9/Optional%20Pre-gate%20Sensor%20(Experimental)

  Similar to the CheeseFrog solution but more complex.  Also requires a teardown/rebuild if added to an existing ERCF.<br />
  <br />

  ### Filamentalist Tensioner Mount based Pre-Gate Sensors

  This option is provided for users who are using an MMU other than ERCF and don't have another option for pre-gate sensors.  Although these work well, I have found that having the sensor "bump" at the beginning of the Tensioner Mount filament path makes filament loading a little more difficult.  If you are building a new ERCF I recommend the Cheesefrog sensors above.  If you have an existing ERCF and have the space for them, the CottontailLite sensors above are a good option.  For more information on the Tesnioner Mount based pre-gate sensor option refer to the assembly manual, CAD, and stl files.

  

  [return to index](#filamentalist-frequently-asked-questions)

## Rubber Band Sourcing Options

### Bike Tire Inner Tube
- You can cut to get a perfect fit across the face of the Rim Roller for 80mm, 100mm, or custom width rewinders with this solution.  Mountain bike or "balloon" tire sized tubes for tires in the 1.75"-2.5" width work well.  Select a wheel diameter of at least 16" to have enough material for up to 12 100mm wide rewinders.  Cut at ~30-35% wider than face of Rim Roller to account for width reduction when stretched onto roller.
  - easy to source locally (your garage, bike shop, hardware store,...)
  - Amazon example: https://www.amazon.com/BELL-Standard-Bicycle-Inner-Tube/dp/B003CUBPUY
  - Aliexpress example: https://www.aliexpress.us/item/3256804654544066.html
 
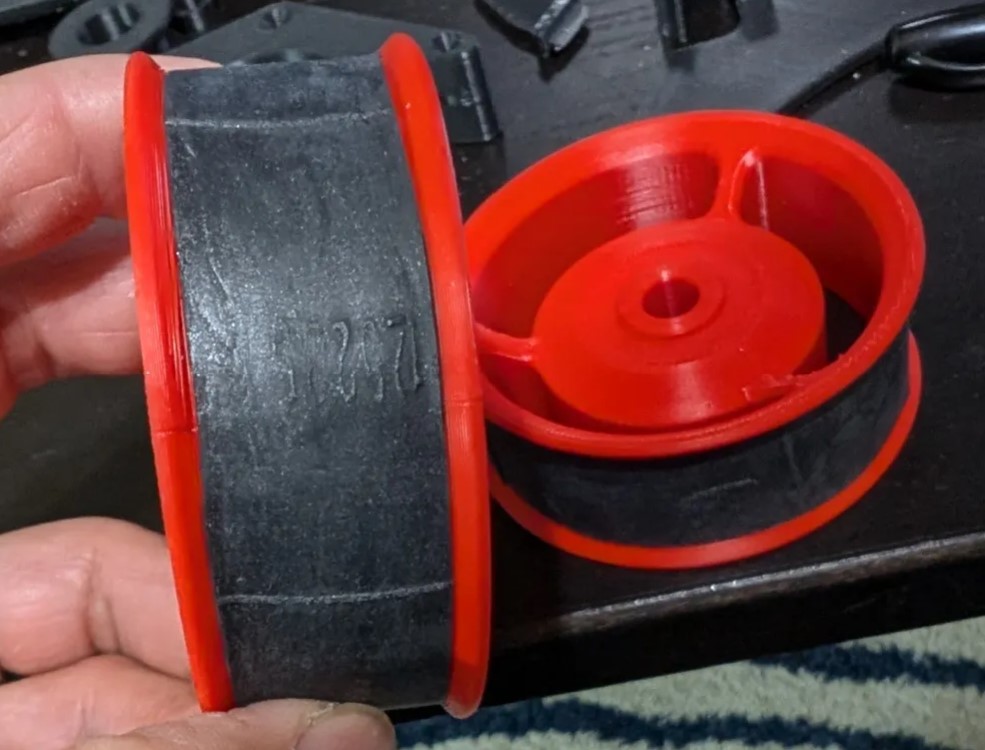
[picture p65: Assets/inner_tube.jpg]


### Rubber Bands
  - For the standard size Classic Rewinder (20mm Rim Roller face width):
    - Size #82 (2 1/2" length x 1/2" wide) or ~50mm diameter (~80mm length) x 10mm width
      - qty 2 per roller for 80mm width version, qty 3 per roller for 100mm width version
    - Amazon example: https://www.amazon.com/AIWOQI-Industrial-supplies-Survival-Tactical/dp/B0CZQ57TF6
    - Aliexpress example: https://www.aliexpress.us/item/3256803949130763.html
  - For the standard size FV3 Rewinder (23mm Rim Roller face width):
    - Size #84 (3 1/2" length x 1/2" wide) or ~57mm diameter (~90mm length) x 12-13mm width
      - qty 2 per roller for 80mm width version, qty 3 per roller for 100mm width version
    - Amazon example: https://www.amazon.com/dp/B0CBJQLXLB
    
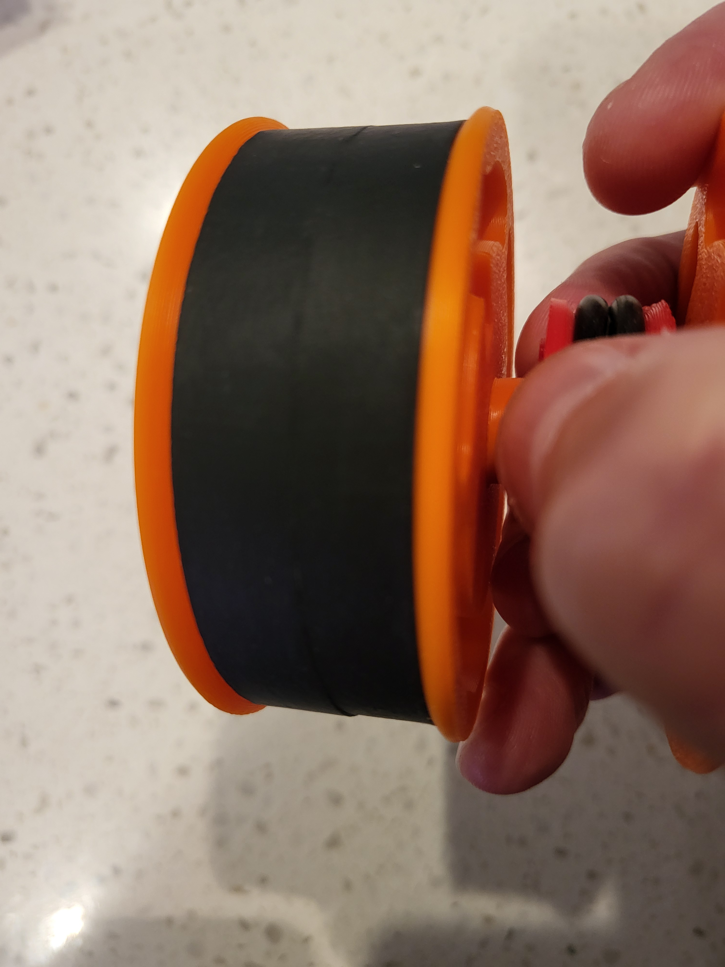
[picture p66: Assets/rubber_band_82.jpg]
<br />
  <br />
    
  [return to index](#filamentalist-frequently-asked-questions)

## Flexible Filament
  - The Filamentalist has been successfully tested with 95A hardness TPU
  - 85A hardness TPU (for example NinjaFlex) - NOT RECOMMENDED! - Soft TPU tends to kink and jam during unload.
  - The smaller/lighter the spool, the better.  The resistance created by the rotational inertia of a heavy spool can cause the Flexibile filament to kink at the o-rings or just expand and jam in the tubing.
    - the little 200/250 gram spools work great.
    - Lower unload acceleration reduces the above problem by reducing the rotational inertia.<br />
  <br />
    
  [return to index](#filamentalist-frequently-asked-questions)

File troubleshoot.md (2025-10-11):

# Filamentalist Troubleshooting Guide

## Debugging Tips for Loose Filament During Rewinder Operation

After a fast load movement, a full spool may rotate a bit further due to inertia and cause a small amount of filament slack around the spool. This behavior is the same as any roller based spool holder and should not cause any issue for printing. 
*In all other Filamentalist operations, there should be no slack forming on the spool.*
If you observe excessive slack, please read the troubleshooting information below.

### Issue: Slack Forming Around the Spool in the Rewind/Unload Direction

**Causes and Solutions:**
- **Tensioner Settings:** Ensure that the tensioner is not overly loose. It should maintain enough tension so that filament movement drives the rollers.
- **One-way Bearing Direction** Check that the bearing is not installed in reverse. See section 3. Drive Roller Assembly in the main readme.md doc.  
- **Spool Slippage:** If the problem occurs when the spool is nearly empty and the spool is slipping on the roller, make sure you have a high traction material such as rubber bands or bicycle inner tube bands on the rim rollers. 

### Issue: Slack Forming Around the Spool in the Print/Load Direction

**Causes and Solutions:**
- **One-Way Bearing Disengagement:** The issue typically indicates that the one-way bearing is failing to switch to free-wheel mode.
  
  **Assembly Checks:**
  - **Spacing and Alignment:** The one-way bearing should not be tightly sandwiched between the two CDR Spacers and Rim Rollers. Instead, the spacers should have a small allowable movement on the shaft (approximately 0.2mm to 0.5mm) .
  
  **Friction Concerns:**

- **Tight One-Way Bearing:** Verify that the one-way bearing rotates freely on the shaft (has equal to, or leass resistance than a 608 bearing). If one-way bearing feels tight/draggy when rotated on the shaft in the unlocked direction the inner plastic spring/retainer my be too tight.  Ttry reworking the bearing using the procedure below:
  - **One-Way Bearing Rework Procedure** - see video of procedure [here](https://photos.app.goo.gl/rgrtAJLfc5br5F7E9)
      1. Place bearing on end of axle rod/tube.
      2. Heat bearing with heat gun or blow dryer until bearing gets hot.  Rotate bearing while heating to get uniform heating
         - **Since power/heat of heat guns vary it is possible to overheat the bearing and melt the inner plastic!** Check result on the first bearing with every 20-30 seconds of heating by following steps c. and d. below until you determine the correct amount of heating required for your heat gun and tight bearings.
      3. While holding the the heated bearing and axle with a towel or (anything to protect your hands from getting burnt), rotate the bearing on the shaft in the unlocked direction until the bearing cools down.
      4. The bearing should now rotate on the axle with little to no resistance in the unlocked direction but still lock tightly in the opposite direction.  If you still feel excessive resistance (greater than a 608 bearing's resistance), repeat the procedure adding even more heat/time.
  - **Lubrication:** Use a light lubricant (thin layer of lithium grease or silicone lubricant) on the center portion of the shaft where the one-way bearing will sit.
  - **5/16" Diameter Axles:**" As a last resort, purchasing 5/16" diameter shaft or stainless steel tubing should result in an axle diameter less than 8mm

## Gear Motor Stalling

**Causes and Solutions:**
- **Excessive Spring Tension on Tensioner Assembly:**  The tensioner screw may be set too tight not allowing the Tensioner Arm to lift and allow for slip when needed
- **Filament Path Resistance:**
  - Excessive filament path length and bends increases system resistance.  Minimize the filament path length and turns between the Filamentalist and the MMU.
  - Increase bowden ID.  2.5mm ID is the recommended diameter for a baseline setup but 3mm ID may be required for long/high-resistance filament paths.
- **Rubbing/Interference of Filamentalist Components:**
  - Remove the filament from the rewinder and spin the Center Drive Roller assembly and the Rear Idler Roller.  Listen and feel for scraping, rubbing, or excessive resistance. If you feel this then the rewinder may need to be dissassembled and reassembled.  When reassembling check that:
    -  the Rim Roller spacing allows the CDR Spacers to free float
    -  the Rear Idler axle screws are not overly tight and causing lateral compresion on the 608 bearing races
    -  the Rim Rollers are not rubbing against anything
    -  the one-way bearing is free of debris

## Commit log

2025-10-11 Initial Carrot-Collective repo setup for the Filamentalist Rewinder
2025-10-11 Initial setup of Filamentalist Rewinder repo for Carrot Collective
    [12mmFrontWheelx2.stl, 12mmRearWheelx2_rev3.stl, 15mmFrontWheelx2.stl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]
2025-10-11 More robust lid latch
    [Latch_Lid.stl]
2026-03-16 Beta CAD V1.2.0 for Testing
    Beta CAD V1.2.0 for testing of Chassis Support polygonal bearing pockets with increased cross sectional area for reduced press-fit stress and greater strength.
2026-03-27 Updated 21 Cup Rubbermaid Dry Box Mounts
    Fix error with alignment pegs that interface with the chassis parts.
    [Rubbermaid_21cup_Dry_Box_Mount_L_[option].stl, Rubbermaid_21cup_Dry_Box_Mount_R_[option].stl]
2026-03-27 Updated 21 Cup Dry Box Mounts
    1. Fixed alignment peg error
    2. Corrected countersunk holes for attaching the 2 halves together
    [Rubbermaid_21cup_Dry_Box_Mount_L_[option].stl, Rubbermaid_21cup_Dry_Box_Mount_R_[option].stl]
